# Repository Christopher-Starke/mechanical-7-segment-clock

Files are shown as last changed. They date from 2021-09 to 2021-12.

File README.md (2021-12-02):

# mechanical-7-segment-clock
A large mechanical 7-segment clock using cheap stepper motors.  

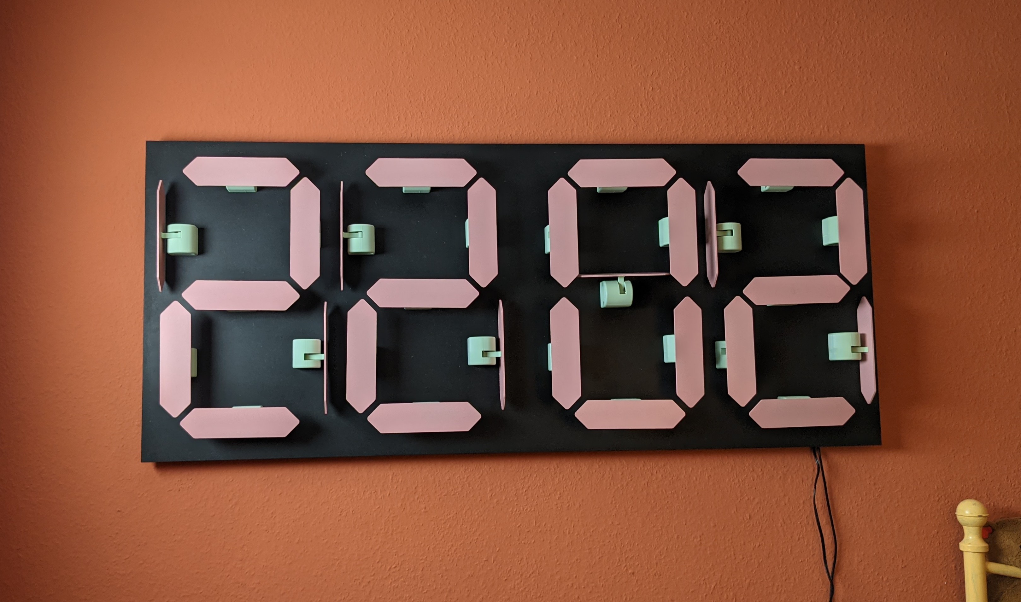
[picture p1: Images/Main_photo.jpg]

##
Each digit requires its own controller board. The seconds digit acts as the master keeping time using the DS3231 RTC and sending I2C commands out to the other digits. The rest of the digits act as slaves receiving numbers via I2C and displaying the number. The minute tens digit needs I2C address #3 hours digit dress #2 and hours tens dress #1. 

## BOM
- 28x		28BYJ-48 5V stepper motors  
- 28x		ULN2003 darlington arrays
- 16x		7HCT 4094 8-bit shift registers 
- 28x		608 skateboard bearings
- 4x		Arduino nano 
- 4x		4 pole screw terminals 
- 1x 		Adafruit ds3231 RTC module
- 56x		M4x10 bolts (for anchoring stepper motors to the housing)
- 56x 		M4x25 bolts (for attaching the stepper casing to the backboard)

### Printed parts 
- 28x		Stepper housings 
- 28x		Levers

### Additional parts
- 1x		Backplate
- 28x		Digit faces

## Assembly
### Stepper motor housing assembly
Assembly of the stepper motor housing can be seen by clicking on the image below. IMAGE ALT TEXT (https://youtu.be/Xs4gIoHIOZU)
Required parts 
- 1x		608 skateboard bearing (yellow)
- 1x		28BYJ-48 5V stepper motor
- 2x 		M4x10 bolts

Printed parts
- 1x 		Lever (red)
- 1x		Stepper Housing (blue)

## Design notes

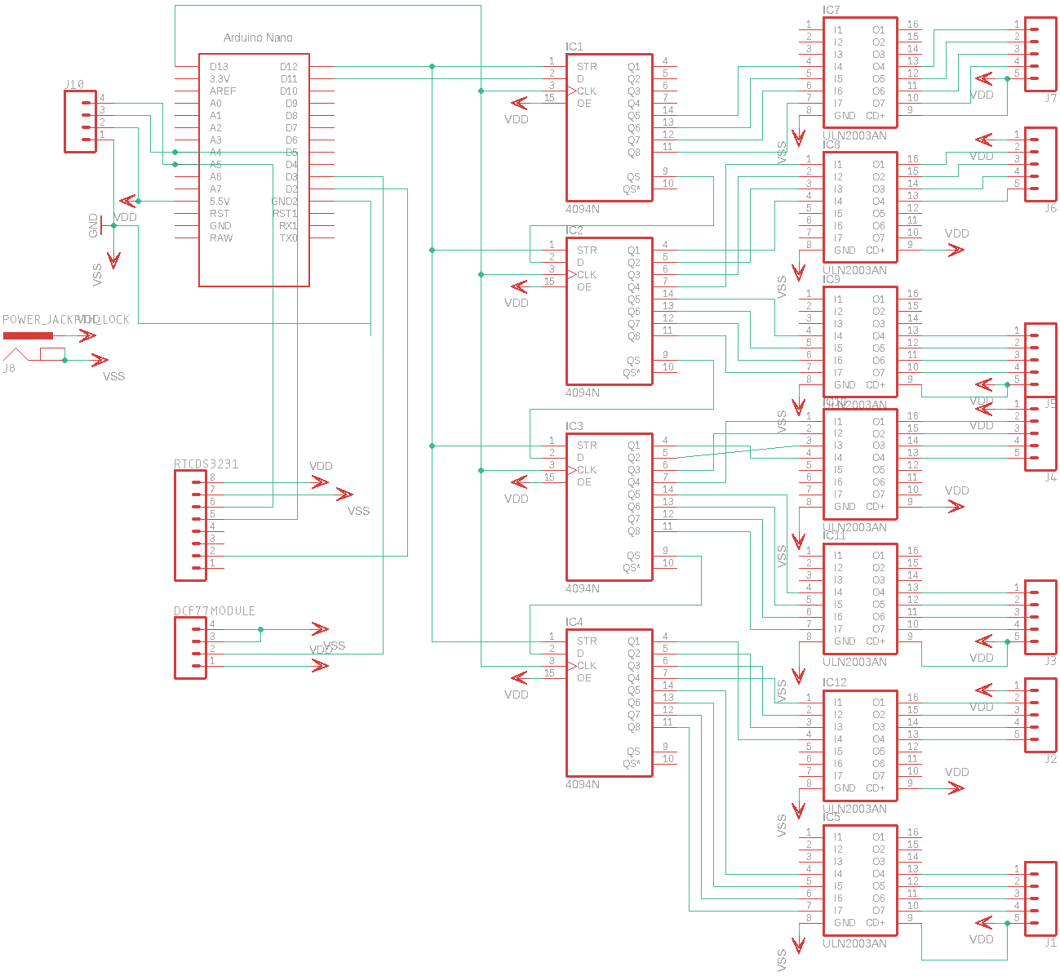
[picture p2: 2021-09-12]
Circuit/Circuit layout.png

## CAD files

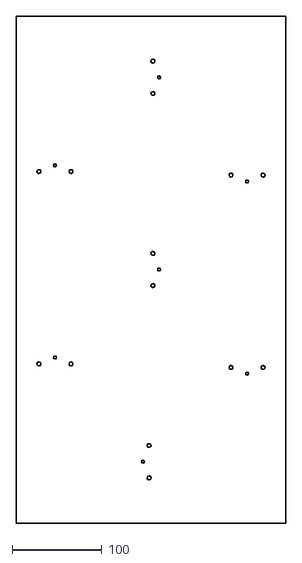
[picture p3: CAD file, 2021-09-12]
Hardware/Dilling template.dxf
300.0 x 565.0

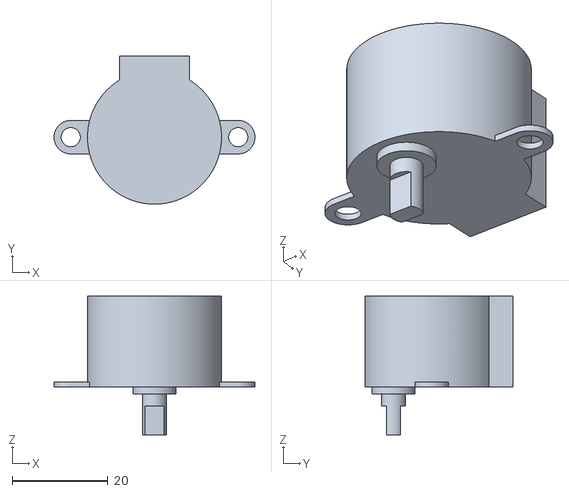
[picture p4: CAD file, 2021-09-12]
Hardware/Stepper assembly/Part Studio 2 - Part 5.stl
42.0 x 31.0 x 29.0

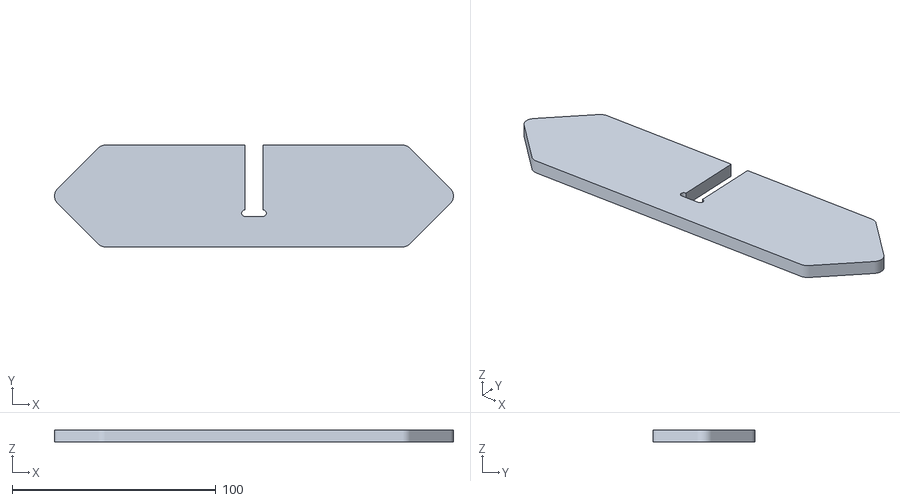
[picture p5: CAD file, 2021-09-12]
Hardware/Segment.stl
195.9 x 50.0 x 6.00

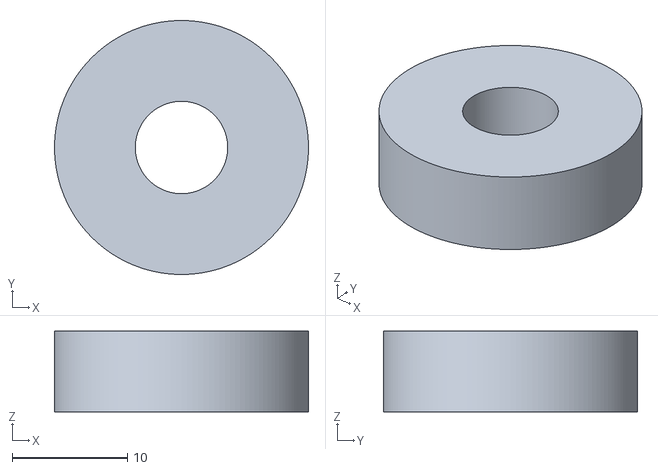
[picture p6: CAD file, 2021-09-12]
Hardware/Stepper assembly/Part Studio 2 - Part 3.stl
22.0 x 22.0 x 7.00

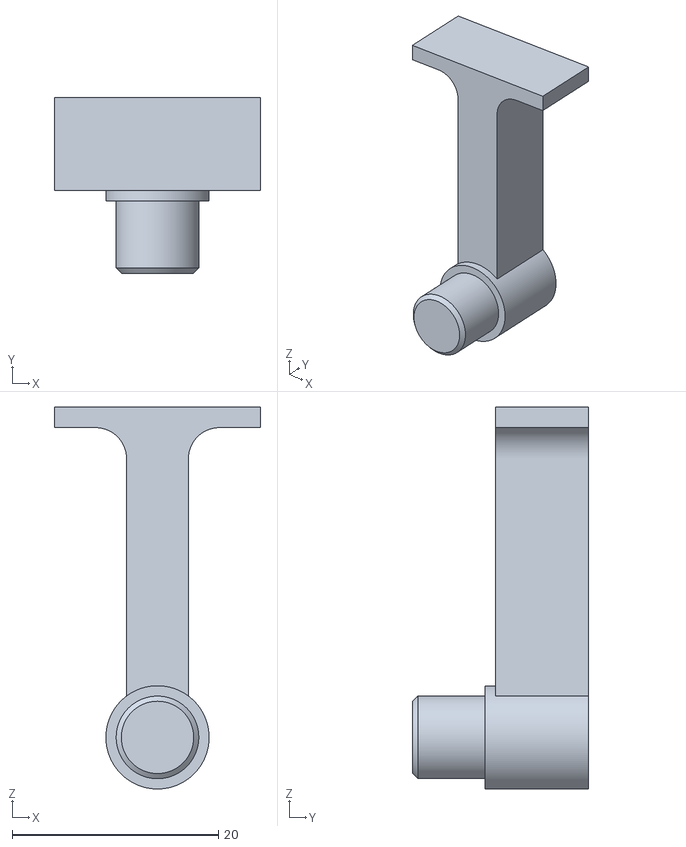
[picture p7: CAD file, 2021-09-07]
Hardware/Lever V3.stl
20.0 x 17.0 x 37.0

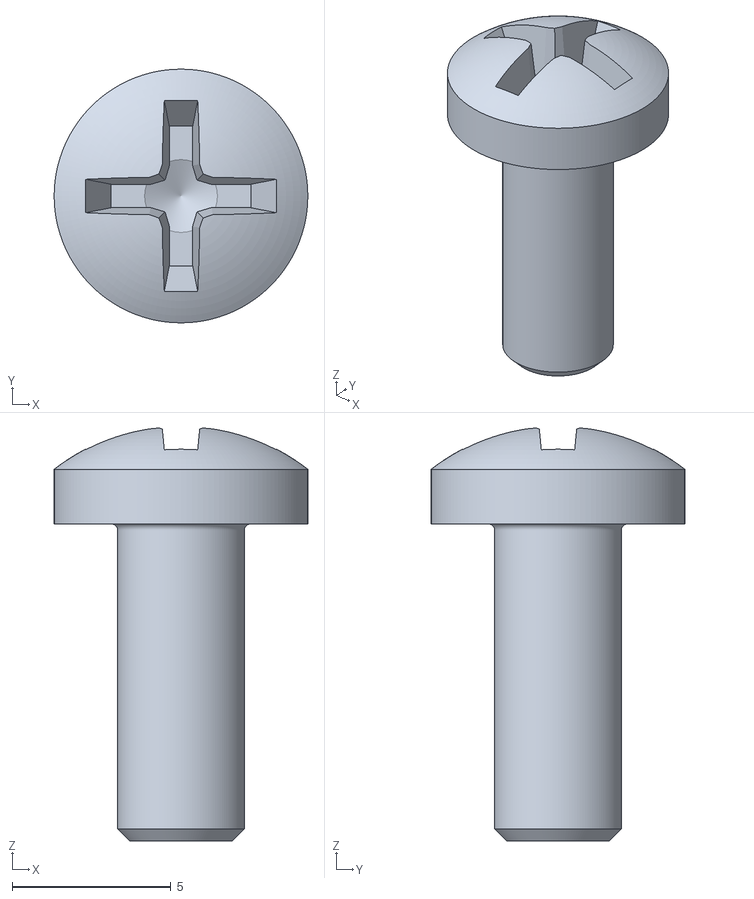
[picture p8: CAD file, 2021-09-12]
Hardware/Stepper assembly/Part Studio 2 - Part 6.stl
8.00 x 8.00 x 13.0

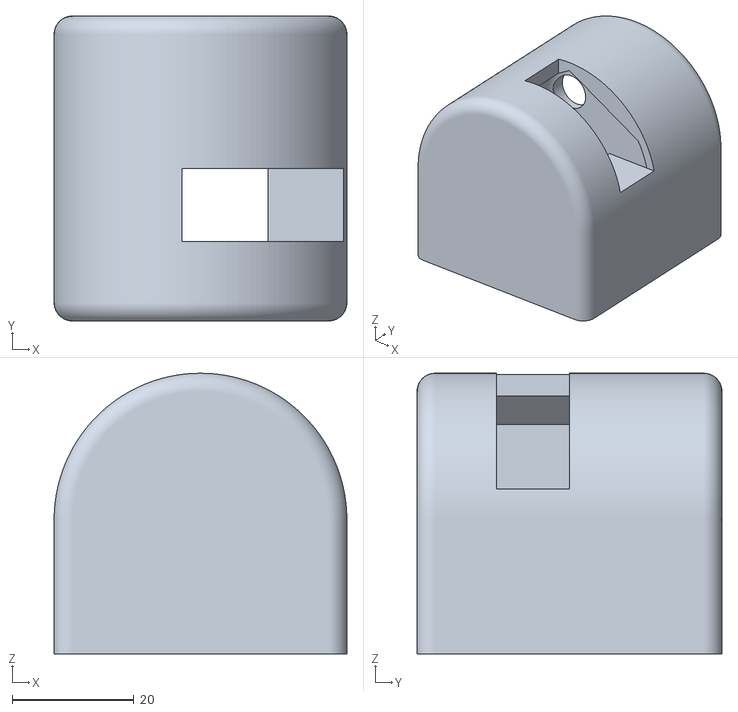
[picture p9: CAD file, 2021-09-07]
Hardware/Case V5-01.stl
48.0 x 50.0 x 46.0

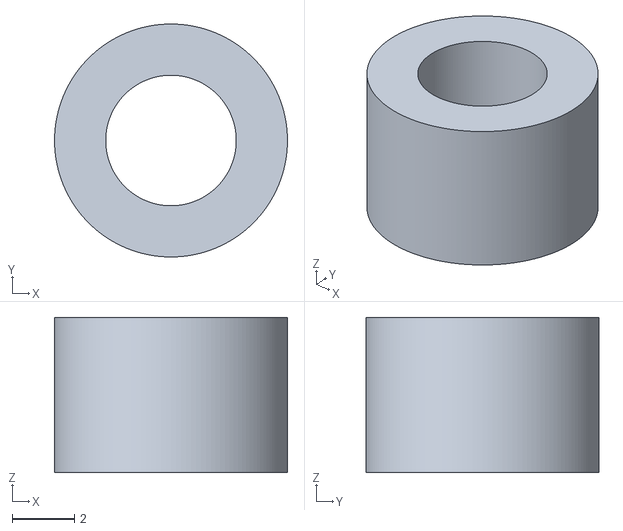
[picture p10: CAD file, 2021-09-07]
Hardware/Standoff.stl
7.50 x 7.50 x 5.00

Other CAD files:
Hardware/Stepper assembly/Part Studio 2 - Part 4.stl
Hardware/Stepper assembly/Part Studio 2 - Part 1.stl
Hardware/Stepper assembly/Part Studio 2 - Part 2.stl
Hardware/Segment.dxf
Hardware/Stepper assembly/Asembley animation.blend

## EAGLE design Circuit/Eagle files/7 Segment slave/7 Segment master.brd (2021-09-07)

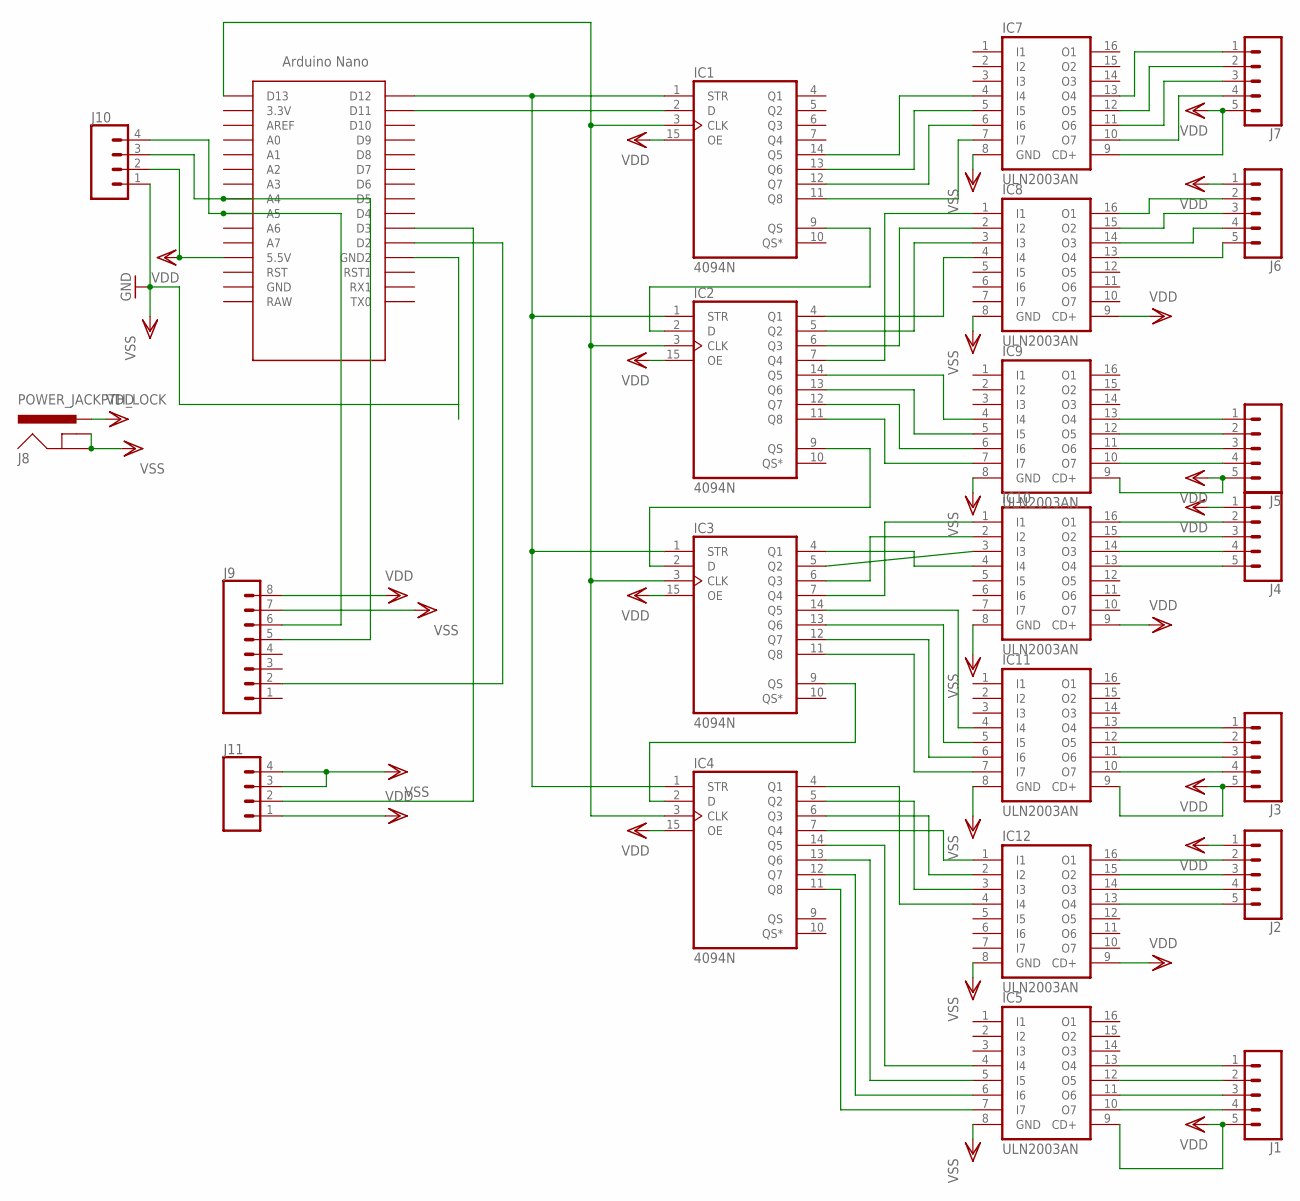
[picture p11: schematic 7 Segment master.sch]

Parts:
IC1, IC2, IC3, IC4: 4094N; DIL16
IC5, IC7, IC8, IC9, IC10, IC11, IC12: ULN2003AN; DIL16
J1, J2, J3, J4, J5, J6, J7: CONN_05LOCK_LONGPADS; 1X05_LOCK_LONGPADS
J8: POWER_JACKPTH_LOCK; POWER_JACK_PTH_LOCK
J9: CONN_08LOCK_LONGPADS; 1X08_LOCK_LONGPADS
J10: CONN_04; SCREWTERMINAL-5MM-4
J11: CONN_04LOCK_LONGPADS; 1X04_LOCK_LONGPADS
U$1: NANO

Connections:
unnamed: IC1.3 (CLK), IC2.3 (CLK), IC3.3 (CLK), IC4.3 (CLK), U$1.D13
unnamed: IC1.2 (D), U$1.D11
unnamed: IC1.9 (QS), IC2.2 (D)
unnamed: IC2.9 (QS), IC3.2 (D)
unnamed: IC1.1 (STR), IC2.1 (STR), IC3.1 (STR), IC4.1 (STR), U$1.D12
unnamed: IC3.9 (QS), IC4.2 (D)
unnamed: IC1.14 (Q5), IC7.4 (I4)
unnamed: IC1.13 (Q6), IC7.5 (I5)
unnamed: IC1.12 (Q7), IC7.6 (I6)
unnamed: IC1.11 (Q8), IC7.7 (I7)
unnamed: IC2.4 (Q1), IC8.4 (I4)
unnamed: IC2.5 (Q2), IC8.3 (I3)
unnamed: IC2.6 (Q3), IC8.2 (I2)
unnamed: IC2.7 (Q4), IC8.1 (I1)
unnamed: IC2.14 (Q5), IC9.4 (I4)
unnamed: IC2.11 (Q8), IC9.7 (I7)
unnamed: IC2.12 (Q7), IC9.6 (I6)
unnamed: IC2.13 (Q6), IC9.5 (I5)
unnamed: IC3.4 (Q1), IC10.4 (I4)
unnamed: IC3.5 (Q2), IC10.3 (I3)
unnamed: IC3.6 (Q3), IC10.2 (I2)
unnamed: IC3.7 (Q4), IC10.1 (I1)
unnamed: IC3.14 (Q5), IC11.4 (I4)
unnamed: IC3.13 (Q6), IC11.5 (I5)
unnamed: IC3.12 (Q7), IC11.6 (I6)
unnamed: IC3.11 (Q8), IC11.7 (I7)
unnamed: IC4.4 (Q1), IC12.4 (I4)
unnamed: IC4.5 (Q2), IC12.3 (I3)
unnamed: IC4.6 (Q3), IC12.2 (I2)
unnamed: IC4.7 (Q4), IC12.1 (I1)
unnamed: IC4.14 (Q5), IC5.4 (I4)
unnamed: IC4.13 (Q6), IC5.5 (I5)
unnamed: IC4.12 (Q7), IC5.6 (I6)
unnamed: IC4.11 (Q8), IC5.7 (I7)
unnamed: IC7.10 (O7), J7.4
unnamed: IC7.11 (O6), J7.3
unnamed: IC7.12 (O5), J7.2
unnamed: IC7.13 (O4), J7.1
unnamed: IC8.16 (O1), J6.2
unnamed: IC8.15 (O2), J6.3
unnamed: IC8.14 (O3), J6.4
unnamed: IC8.13 (O4), J6.5
unnamed: IC9.13 (O4), J5.1
unnamed: IC9.12 (O5), J5.2
unnamed: IC9.11 (O6), J5.3
unnamed: IC9.10 (O7), J5.4
unnamed: IC10.16 (O1), J4.2
unnamed: IC10.15 (O2), J4.3
unnamed: IC10.14 (O3), J4.4
unnamed: IC10.13 (O4), J4.5
unnamed: IC11.13 (O4), J3.1
unnamed: IC11.12 (O5), J3.2
unnamed: IC11.11 (O6), J3.3
unnamed: IC11.10 (O7), J3.4
unnamed: IC12.16 (O1), J2.2
unnamed: IC12.15 (O2), J2.3
unnamed: IC12.14 (O3), J2.4
unnamed: IC12.13 (O4), J2.5
unnamed: IC5.13 (O4), J1.1
unnamed: IC5.12 (O5), J1.2
unnamed: IC5.11 (O6), J1.3
unnamed: IC5.10 (O7), J1.4
unnamed: J9.6, J10.4, U$1.A5
unnamed: J9.5, J10.3, U$1.A4
unnamed: J9.2, U$1.D2
unnamed: J11.2, U$1.D3
VDD: IC1.15 (OE), IC1.16 (VDD), IC2.15 (OE), IC2.16 (VDD), IC3.15 (OE), IC3.16 (VDD), IC4.15 (OE), IC4.16 (VDD), IC5.9 (CD+), IC7.9 (CD+), IC8.9 (CD+), IC9.9 (CD+), IC10.9 (CD+), IC11.9 (CD+), IC12.9 (CD+), J1.5, J2.1, J3.5, J4.1, J5.5, J6.1, J7.5, J8.PWR, J9.8, J10.2, J11.1, U$1.5V (5.5V)
VSS: IC1.8 (VSS), IC2.8 (VSS), IC3.8 (VSS), IC4.8 (VSS), IC5.8 (GND), IC7.8 (GND), IC8.8 (GND), IC9.8 (GND), IC10.8 (GND), IC11.8 (GND), IC12.8 (GND), J8.GND, J8.GNDBREAK, J9.7, J10.1, J11.3, J11.4, U$1.GND1 (GND2)

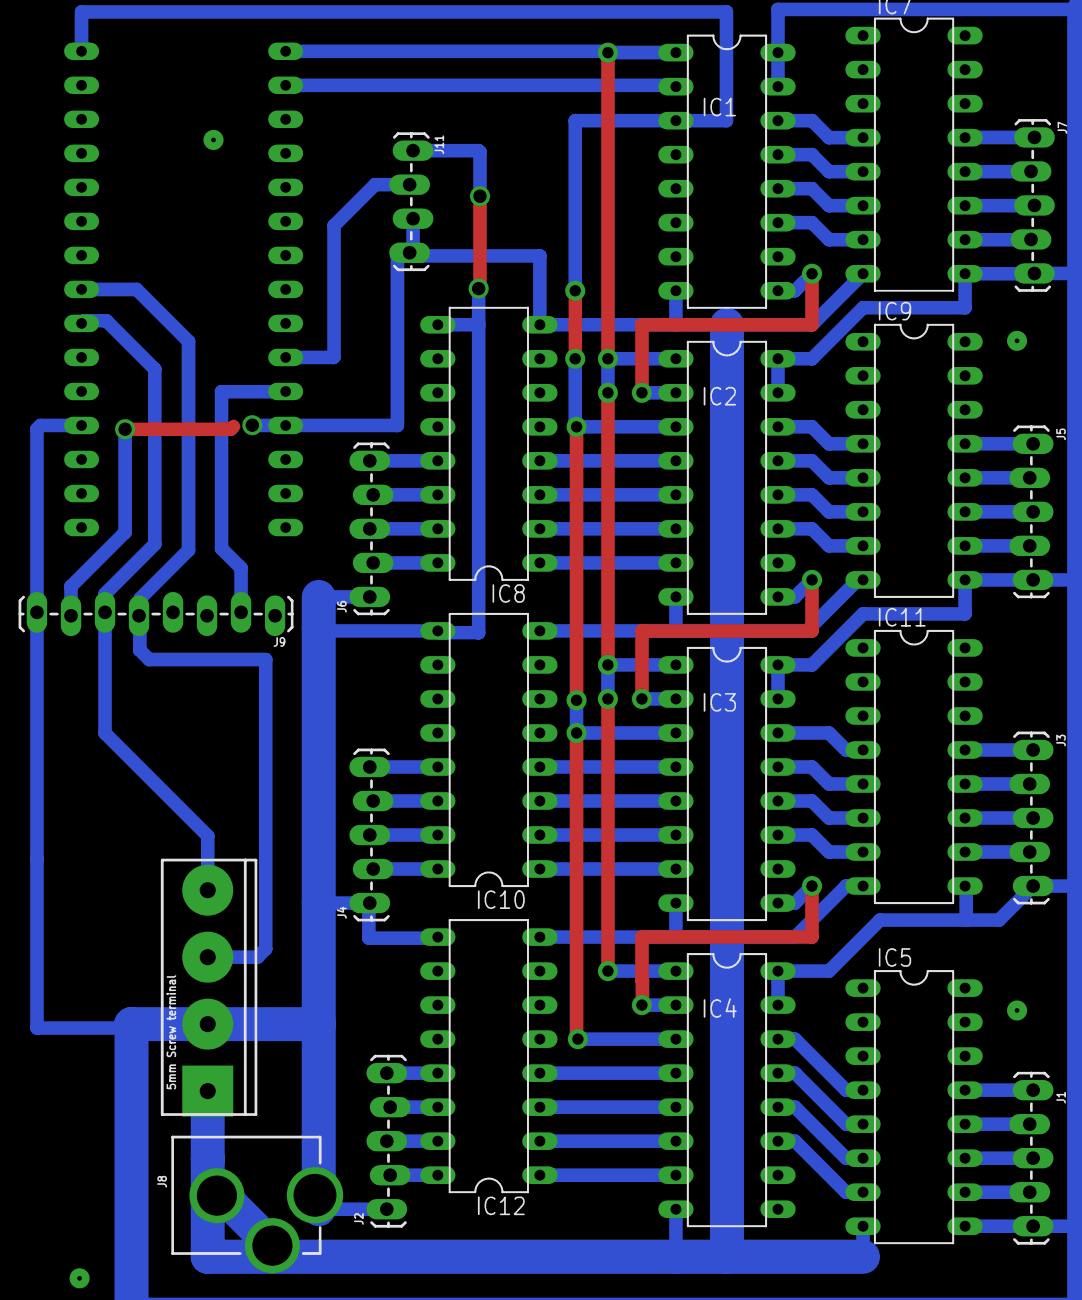
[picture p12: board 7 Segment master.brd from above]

Board: 2 copper layers, 23 parts (0 on the bottom side), 68 nets.

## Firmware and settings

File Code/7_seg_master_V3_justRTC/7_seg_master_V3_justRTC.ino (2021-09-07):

#include <SPI.h>
#include <Wire.h>
uint8_t newNumber = 10;
uint8_t oldNumber = 8;
uint8_t segmentOrder[11] = {0b01111110, 0b00110000, 0b01101101, 0b01111001, 0b00110011, 0b01011011, 0b01011111, 0b01110000, 0b01111111, 0b01111011, 0b00000001}; //
const uint32_t stepOrder[9] = {0b00000000,0b00000001, 0b00000011, 0b00000010, 0b00000110, 0b00000100,0b00001100,0b00001000,0b00001001}; //binary order for stepper movement
int8_t currentStep[7] = {1, 1, 1, 1, 1, 1, 1};
uint32_t newBitOut = 0b10000000000000000000000000000000;
uint32_t stepsPerMove = 1100; /// set correctly 4096/rev
uint32_t stepRate = 1;
uint32_t mask;
const int slaveSelectPin = 12;
uint32_t timer;


byte Minutes       = 0;
byte minuteDigit   = 0;
byte minuteTens    = 0;
byte Hours         = 0;
byte hourDigit     = 0;
byte hourTens      = 0;

// slave select 10 connected to RCLCK - strobe STR
// SCK 13 to SRCLCK CP
// MOSI 11 to SER in D
// 5V to OE

#include "RTClib.h"

RTC_DS3231 rtc;
#define CLOCK_INTERRUPT_PIN 2


void setup() {
  pinMode(slaveSelectPin, OUTPUT);
  SPI.beginTransaction(SPISettings(500000, LSBFIRST, SPI_MODE0)); 
  SPI.begin();
  Serial.begin(9600);
 
  moveStepper( -1 , segmentOrder[oldNumber] ); //Reset the clock to open position
  oldNumber = newNumber;
  moveStepper( 1, segmentOrder[newNumber]);
  
  
    if (! rtc.begin()) {
    Serial.println("Couldn't find RTC");
    Serial.flush();
    abort();
  }

   /* if (rtc.lostPower()) {
    Serial.println("RTC lost power, let's set the time!");
    // When time needs to be set on a new device, or after a power loss, the
    // following line sets the RTC to the date & time this sketch was compiled
    rtc.adjust(DateTime(0,0,0, 14, 30,00));
    // This line sets the RTC with an explicit date & time, for example to set
    // January 21, 2014 at 3am you would call:
    // rtc.adjust(DateTime(2014, 1, 21, 3, 0, 0));
  }*/     

   rtc.adjust(DateTime(0,0,0,15, 16,00)); // sets the time on reset 

    //we don't need the 32K Pin, so disable it
    rtc.disable32K();
    
    // Making it so, that the alarm will trigger an interrupt
    pinMode(CLOCK_INTERRUPT_PIN, INPUT_PULLUP);
    attachInterrupt(digitalPinToInterrupt(CLOCK_INTERRUPT_PIN), onAlarm, FALLING);
    
    // set alarm 1, 2 flag to false (so alarm 1, 2 didn't happen so far)
    // if not done, this easily leads to problems, as both register aren't reset on reboot/recompile
    rtc.clearAlarm(1);
    rtc.clearAlarm(2);
    
    // stop oscillating signals at SQW Pin
    // otherwise setAlarm1 will fail
    rtc.writeSqwPinMode(DS3231_OFF);
    
    // turn off alarm 2 (in case it isn't off already)
    // again, this isn't done at reboot, so a previously set alarm could easily go overlooked
    rtc.disableAlarm(2);
    
    // schedule an alarm at the next minute seconds in the future
    rtc.setAlarm1(DateTime(0,0,0,0,0,00),DS3231_A1_Second);
  
}

void loop() {

  if(rtc.alarmFired(1)){

    DateTime now = rtc.now();
    Serial.println(now.minute(),DEC);
    rtc.clearAlarm(1);
    rtc.setAlarm1(DateTime(0,0,0,0,0,00),  DS3231_A1_Second );

     Minutes      = now.minute();
  minuteTens  = Minutes / 10;
  minuteDigit = Minutes - minuteTens * 10;

  Hours       = now.hour();
  hourTens    = Hours / 10;
  hourDigit   = Hours - hourTens * 10;

  newNumber = minuteDigit;

  Wire.beginTransmission(3); // transmit to device #3
  Wire.write(minuteTens);              // sends one byte
  Wire.endTransmission();    // stop transmitting

  Wire.beginTransmission(2); // transmit to device #2
  Wire.write(hourDigit);              // sends one byte
  Wire.endTransmission();    // stop transmitting

  Wire.beginTransmission(1); // transmit to device #1
  Wire.write(hourTens);              // sends one byte
  Wire.endTransmission();    // stop transmitting

    Serial.println(newNumber);
  Serial.println(segmentOrder[newNumber],BIN ); 
  moveStepper( -1 , segmentOrder[oldNumber]);  // move segments to new position  
  oldNumber = newNumber;
  moveStepper( 1 , segmentOrder[newNumber] ); 
 
    // move all segments to open position
    
    
  }
   

    

  
}



void moveStepper(int dir, int segments) {

  int stepsToGo = stepsPerMove;
  while (stepsToGo > 0 ) {
    int segment = 0;
    while ( segment < 8 ) {
    //Serial.println("step");
    
      if (bitRead(segments, segment) == 1) {
        currentStep[segment] = currentStep[segment] + dir; //increment in desired direction
        if (currentStep[segment] == 9)  {
          currentStep[segment] = 1; //rollover
        }
        if (currentStep[segment] == 0) {
          currentStep[segment] = 8; //rollover
        }
        
        uint32_t mask = 0b1111ul <<  4*segment;        
        newBitOut = ~mask & newBitOut; //overwrite the 4 bit piece we want to rewrite
        newBitOut = newBitOut | stepOrder[currentStep[segment]] << 4 * segment; 
        //Serial.println(newBitOut,BIN);
      }
      
      segment++;
      
    }

        digitalWrite (slaveSelectPin,  HIGH);
        SPI.transfer(newBitOut);
        SPI.transfer(newBitOut>>8);  
        SPI.transfer(newBitOut>>16); 
        SPI.transfer(newBitOut>>24);     
        digitalWrite (slaveSelectPin, LOW);

    stepsToGo = stepsToGo - 1;
    while (millis() <= timer + stepRate){
      ;
    }
    timer = millis();
  }

}

void onAlarm() { //minuteAlarm
    Serial.println("Alarm occured!");
    
}

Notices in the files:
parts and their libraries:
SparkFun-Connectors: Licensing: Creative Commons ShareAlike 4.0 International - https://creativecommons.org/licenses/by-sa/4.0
